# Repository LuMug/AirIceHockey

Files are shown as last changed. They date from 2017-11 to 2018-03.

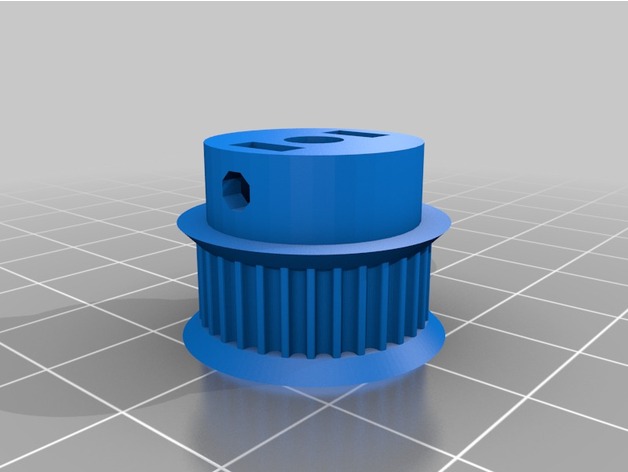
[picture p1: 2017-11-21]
Documenti_Esterni/Evo_Parts/images/PULEGGIA_MOTORE.jpg

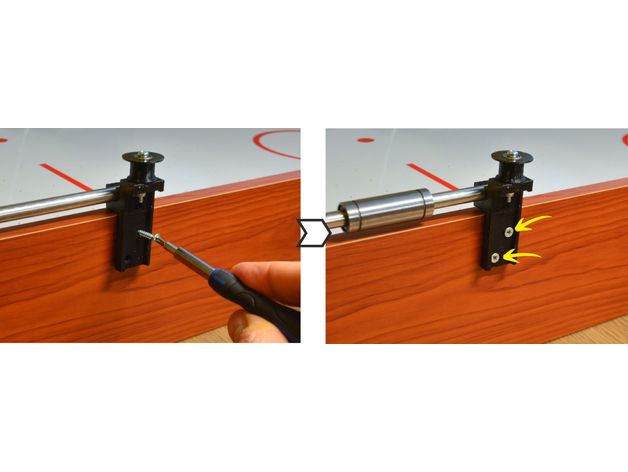
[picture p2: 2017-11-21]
Documenti_Esterni/Evo_Parts/images/Particolare_Supporto_Pulegge.jpg

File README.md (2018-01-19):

# Air Ice Hockey
### Descrizione
Si tratta di realizzare un gioco di Air Ice Hockey che permetta ad un giocatore di giocare contro un sistema robotizzato costituito da due motori passo-passo controllati da un Arduino.
Arduino riceve i comandi da un programma di visione 3D tramite una web cam oppure sfruttando un’applicazione su uno smartphone e la camera dello stesso.
### Docenti Responsabili
* Luca Muggiasca
* Adriano Barchi
### Lavoratori
* Alessia Sarak
* Joey Biancardi
* Alessandro Spagnuolo
* Giairo Mauro
## Info
**Inizio:** 10.11.2017  
**Consegna:** 19.01.2018
* [Documentazione](https://github.com/LuMug/AirIceHockey/tree/master/Documenti_Esterni "Cartella documentazione")
  + [Quaderno dei compiti](https://github.com/LuMug/AirIceHockey/blob/master/Documenti_Esterni/qdc_p2_samt_2017_18-Ice_Hockey_Robot.docx "Quaderno dei compiti")
  + [Motori passo-passo](https://github.com/LuMug/AirIceHockey/tree/master/Documenti_Esterni/Stepper_Motors "Cartella motori passo passo")
  + [Foto di montaggio](https://github.com/LuMug/AirIceHockey/tree/master/Documenti_Esterni/Evo_Parts/images "Montaggi")
* [Programmi Arduino](https://github.com/LuMug/AirIceHockey/tree/master/Programmi%20Arduino%20-%20Motori%20e%20WiFi "Cartella programmi")
  + [Programma JJRobots](https://github.com/LuMug/AirIceHockey/tree/master/Programmi%20Arduino%20-%20Motori%20e%20WiFi/AHRobot_EVO "Programma JJRobots")
  + [Programma timer](https://github.com/LuMug/AirIceHockey/blob/master/Programmi%20Arduino%20-%20Motori%20e%20WiFi/timer.ino "Programma timer")
  + [Schema elettrico timer](https://github.com/LuMug/AirIceHockey/blob/master/Programmi%20Arduino%20-%20Motori%20e%20WiFi/timer_schema.fzz "Schema elettrico timer")
* [Trello Project Management](https://trello.com/b/uI6cxGCE/airicehockey "Trello")
* [GitHub Repository](https://github.com/LuMug/AirIceHockey "GitHub Progetto")
## Diari
* [Diari](https://github.com/LuMug/AirIceHockey/tree/master/Diari "Diari")

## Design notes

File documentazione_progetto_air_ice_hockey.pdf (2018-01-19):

### Scuola Arti e Mestieri Trevano

### Sezione informatica

Titolo del progetto: | Air Ice Hockey
Alunni: | Alessia Sarak, Giairo Mauro, Joey Biancardi, Alessandro Spagnuolo
Classe: | Info I3
Anno scolastico: | 2017/2018
Docenti responsabili: | Luca Muggiasca e Adriano Barchi

# Air Ice Hockey

### SAMT – Sezione Informatica

Pagina 2 di 17

### Air Ice Hockey

Alessia, Giairo, Joey, Alessandro | Air Ice Hockey | Versione: 19.01.2018

Pagina 3 di 17

### 1 Introduzione

### 1.1 Informazioni sul progetto

Il progetto consiste nel fare un campo da Air Ice Hockey dove l’avversario è il computer. Esso deve saper rispondere all’avversario in tempo reale.
Il gruppo responsabile del progetto è composto da:
- Alessia Sarak della I3AA
- Giairo Mauro della I3BB
- Joey Biancardi della I3BB
- Alessandro Spagnuolo della I3BB
I docenti responsabili del progetto sono Adriano Barchi e Luca Muggiasca.

### 1.2 Abstract

The purpose of this project is to have an ice air hockey table that function.
This game is compost of two players; one is the computer and one is the person. The Computer part will be programming with Arduino mega.
There is an application that already exist (JJRobots), it will take the data of the table and the disk and, with Wi-Fi connection, it will send all data on our program. The data will be interpreted from the program and then the program will make his move. This move must be instantaneous and the program must decide which strategy use. There are 3 strategies: attack, defence and attack and defence.
The computer will answer in real time.

### 1.3 Scopo

Lo scopo del progetto è di creare un campo funzionante di Air Ice Hockey. Il gioco è composto da due giocatori: il computer e la persona.
Il computer dev’essere in grado di rispondere ai colpi dell’avversario in tempo reale tramite una webcam che legge i valori del disco e calcola la direzione in cui andrà, in questo modo riesce a capire dove muovere il robot, in modo che sia del tutto autonomo una volta fatta partire l’applicazione.

Analisi

### 1.4 Analisi del dominio

Abbiamo un campo da air hockey classico per 2 giocatori.
Quello che dobbiamo creare è già stato creato come progetto, JJRobots, e noi dobbiamo replicarlo usando i pezzi che i professori ci hanno dato.
L’idea del progetto è presentarlo a espoprofessioni agli interessati alla nostra scuola e in particolare alla nostra sezione (Scuola Arti e Mestieri di Trevano, sezione informatici).
Ci sarà un solo giocatore che si sfida con un sistema robotizzato che si muove grazie ad Arduino. Il come è spiegato nella sezione “scopo” e nel capitolo “implementazione”.
Per poter implementare questo progetto bisogna avere delle buone conoscenze su Arduino e bisogna conoscere come far funzionare i motori con la scheda di JJRobots per poi poterle applicare alla programmazione.

Pagina 4 di 17

### 1.5 Analisi e specifica dei requisiti

ID | REQ-001
Nome | Tavolo
Priorità | 1
Versione | 1.0
Note | -
Sub-ID | Sviluppo
001 | I componenti che muovono il robot sono montati e funzionali
002 | Accanto al punteggio c'è il segnatore di tempo rimanente
ID | REQ-002
Nome | Strategie di gioco
Priorità | 1
Versione | 1.0
Note | -
Sub-ID | Programmazione
001 | Nel programma devono essere presenti 3 strategie di gioco
002 | Strategia 1: Difesa
003 | Strategia 2: Attacco
004 | Strategia 3: Difesa - Attacco
ID | REQ-003
Nome | Movimento computer
Priorità | 1
Versione | 1.0
Note | -
Sub-ID | Programmazione
001 | Il telefono che inquadra il campo da gioco deve essere collegato con il programma
002 | Vengono registrati i dati del disco in movimento
003 | I dati vengono utilizzati per definire quale strategia di gioco utilizzare
004 | Viene attivata la strategia di gioco

### 1.6 Pianificazione

Il Gannt è suddiviso in giorni e ogni giorno è diviso in tre: le prime 2 ore, le seconde 2 ore e le terze 2 ore. Ogni colore rappresenta un membro del gruppo; il rosa rappresenta Alessia Sarak, il verde rappresenta Joey Biancardi, il blu rappresenta Giairo Mauro e il giallo rappresenta Alessandro Spagnuolo.
Il 19 gennaio è libero nel caso di qualche ritardo o nel caso si volesse perfezionare qualcosa.

Pagina 5 di 17

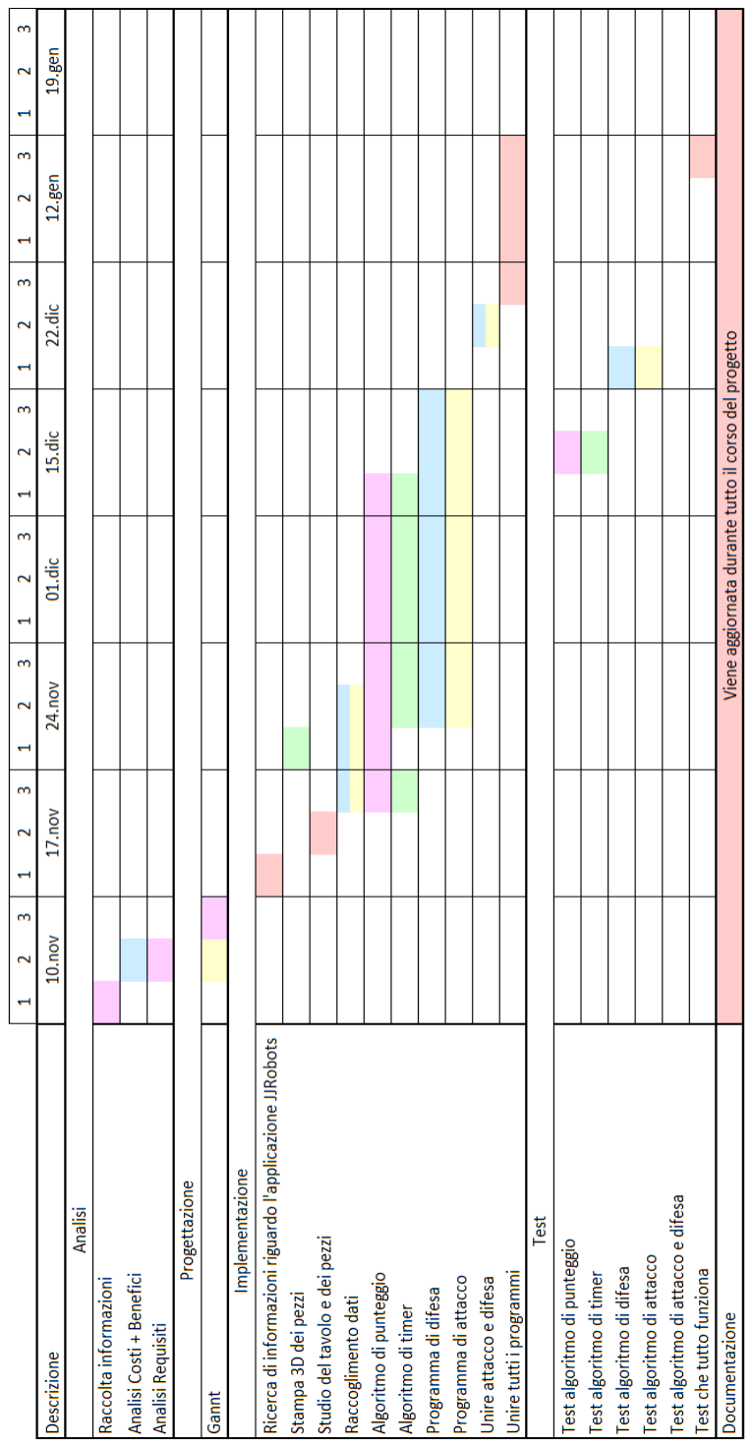
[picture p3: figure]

Pagina 6 di 17

### 1.7 Analisi dei mezzi

A disposizione c’è un tavolo per il gioco, la stampante 3D per stampare i pezzi da montare sul tavolo, l’applicazione JJRobots per prendere le misure del tavolo, una 7 segmenti Adafruit per segnalare il tempo alla fine del gioco e il nostro portatile.

### 1.7.1 Software

- Arduino IDE (programma)
- AHR Robot (JJRobots)
- Word (documentazione e diari)
- Excel (Gannt)
- Google Chrome (come visualizzatore di pdf e per le ricerche)
- PowerPoint (presentazione)
- Fritzing (schema montaggio di arduino)

### 1.7.2 Hardware

Il prodotto verrà sviluppato su un campo da Air Ice Hockey. La base è identica a quella di un campo normale, la differenza sta nel campo dell’avversario che, essendo computerizzato, ha un pusher montato su delle sbarre, esse sono collegate a delle cinghie. Per permettere il movimento del pusher sono necessari anche la scheda di JJRobots, 2 motori passo-passo, e per definire la direzione del movimento si necessita di un telefono (sistema operativo android) che tramite l’applicazione di JJRobots (Air Hockey) riesce a prevedere il movimento che verrà fatto dal puck.

Lista dei pezzi utilizzati (per vedere come montarli tra di loro andare sotto implementazione, pagina 7):
- Tavolo
- 1 – Tavolo da Air Ice Hockey
- 2 – Pusher
- 1 – Puck
- 2 – Sbarre
- 1 – Cinghia
- 2 – Motori passo-passo
- 1 – Telefono (sistema operativo Android) con su l’applicazione di JJRobots (Air Hockey)
- Timer
- 1 – Arduino Uno
- 1 – 7 segmenti Adafruit
- 2 – Resistenze
- 1 – Led Blu
- 1 – Bottone
- Programma con Arduino
- Arduino Leonardo

Pagina 7 di 17

### 2 Implementazione

Per poter fare il tavolo di Air Ice Hockey funzionante il lavoro è stato suddiviso in 3 parti: motori, algoritmo di timer e montaggio del tavolo, rispettivamente ci hanno lavorato Giairo Mauro e Alessandro Spagnuolo, Alessia Sarak, Joey Biancardi.

Motori

Componenti utilizzati

- 1 Arduino Mega (serve Arduino Leonard)
- 2 motori Stepper Motor
- 2 A4988 Stepper Motor Driver
- 1 Scheda JJRobots

Montaggio

Abbiamo montato un radiatore su ogni Driver per evitare il riscaldamento di essi, una volta fatto abbiamo collegato i due driver alla scheda JJRobots.

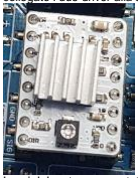
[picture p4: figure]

I cavi del motore sono stati saldati a dei componenti e poi collegati alla scheda, i cavi sono stati saldati secondo un ordine preciso mostrato nel Datasheet dei motori.

Una volta finito il montaggio della scheda JJRobots l’abbiamo collegata all’arduino fornitoci (arduino mega 2560) come mostrato nella foto seguente.

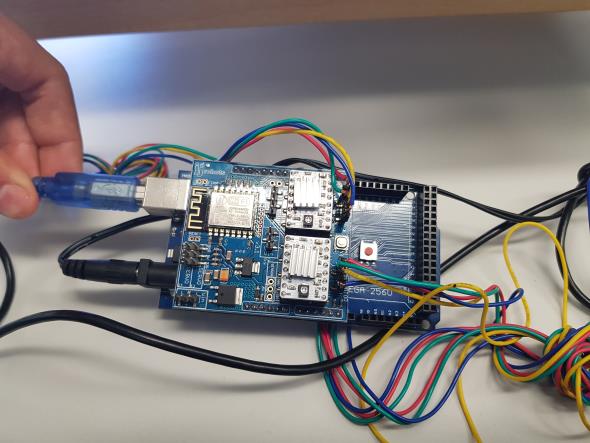
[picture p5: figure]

Pagina 8 di 17

Test motori
Attributi:
- | const int enaM1M2Pin = 4; | → pin per l’abilitazione dei due motori
- | const int microStepPin = A4; | → pin per suddivisione dei passi in micro passi
- | const int pushButtonPin = A3; | → pin per il Pulsante sul board
- | int Val = 0; | → variabile per la lettura pulsante
- | const int stepM1Pin = 7; | → Pin per step motore 1
- | const int dirM1Pin = 8; | → Pin per direzione motore 1
- | const int stepM2Pin = 12; | → Pin per step motore 2
- | const int dirM2Pin = 5; | → Pin per direzione motore 2
Il programma fa fare un giro in avanti e uno indietro ai motori, ma se si preme il bottone presente sulla scheda JJRobots fa solo un giro in una direzione.

digitalWrite(dirM1Pin, HIGH); → Inizialmente si abilita la direzione in cui si vogliono muovere i motoricon questo comando: con “HIGH” si muove in avanti con “LOW” si muove indietro.

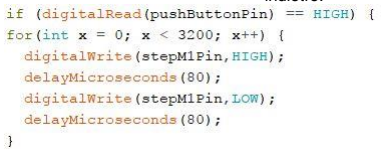
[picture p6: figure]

→ | Con il primo if si dice che quando si preme il bottone i motori devono muoversi anche in avanti.

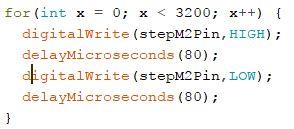
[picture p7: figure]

→ | In questo for si fa girare il motore per un gio conpleto con 3200 impulsi.

Con questi codici si può creare il progetto.

Programma per JJRobots

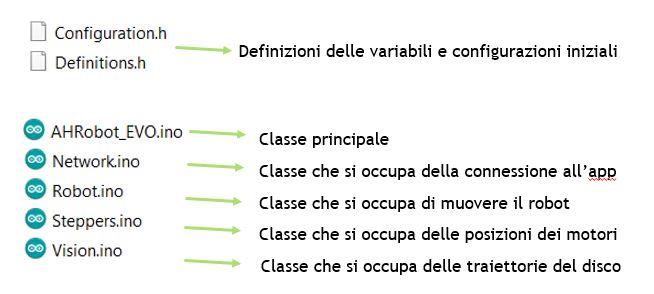
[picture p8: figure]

Le classi utilizzate per il progetto le abbiamo scaricate dal sito di JJRobots e sono le seguenti:

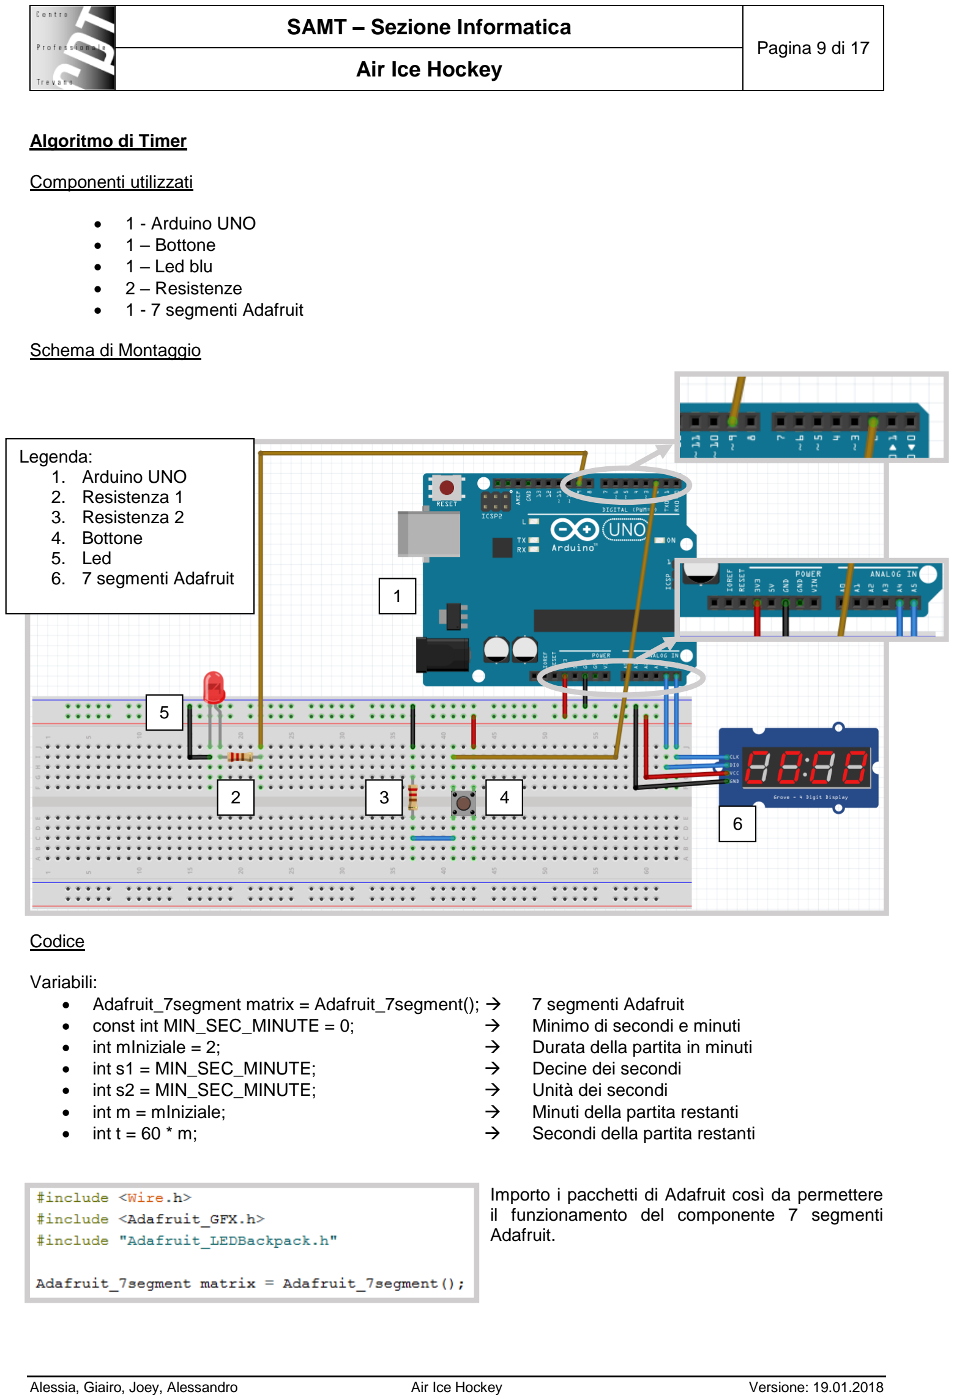
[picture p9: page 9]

Pagina 9 di 17

Algoritmo di Timer

Componenti utilizzati

- 1 - Arduino UNO
- 1 – Bottone
- 1 – Led blu
- 2 – Resistenze
- 1 - 7 segmenti Adafruit

Schema di Montaggio

Codice

Variabili:
- | Adafruit_7segment matrix = Adafruit_7segment(); → | 7 segmenti Adafruit
- | const int MIN_SEC_MINUTE = 0; | → | Minimo di secondi e minuti
- | int mIniziale = 2; | → | Durata della partita in minuti
- | int s1 = MIN_SEC_MINUTE; | → | Decine dei secondi
- | int s2 = MIN_SEC_MINUTE; | → | Unità dei secondi
- | int m = mIniziale; | → | Minuti della partita restanti
- | int t = 60 * m; | → | Secondi della partita restanti

Importo i pacchetti di Adafruit così da permettere il funzionamento del componente 7 segmenti Adafruit.

5

2

1

3 | 4
6

Legenda:
1. Arduino UNO
2. Resistenza 1
3. Resistenza 2
4. Bottone
5. Led
6. 7 segmenti Adafruit

5

6

1

2 | 3 | 4

Pagina 10 di 17

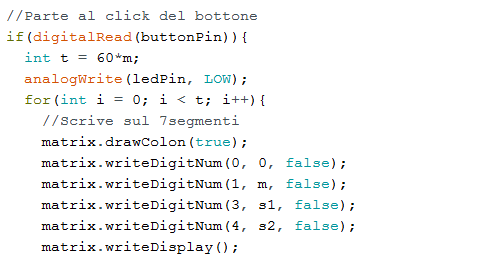
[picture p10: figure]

Quando il bottone viene schiacciato parte il conto alla rovescia.
Spengo il led che segna la fine della partita.
Il for si ripete per il numero di secondi necessari.

matrix.drawColon(bool);
Definisce se i due punti “ : “ devono venire segnati o meno.

matrix.writeDigit(colonna, numero 0 – 9, bool); Colonna: in quale casella devo scriverci su. Numero: valore da scriverci.
Bool: se il punto del rispettivo numero è acceso o spento.

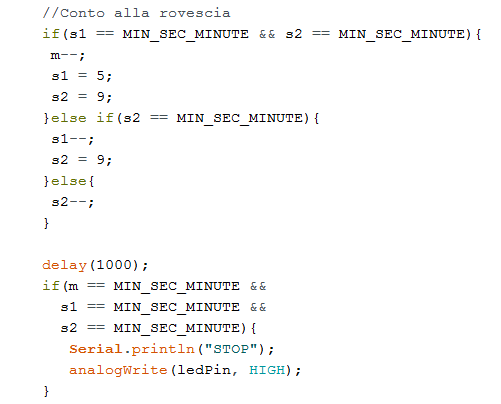
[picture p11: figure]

Faccio il conto alla rovescia sottraendo i vari valori; quando sono tutti a 0 si ferma il tempo, quando i secondi (s1, s2) vanno a 0 si sottrae un minuto (m) al tempo totale, se le unità (s2) vanno a 0 si sottrae uno alle decine (s1) e si fa tornare le unità a 9, altrimenti si sottrae uno alle unità (s2).

Delay(1000) serve per far passare un secondo tra una sottrazione e l’altra.

Finito il delay controllo se il tempo è finito e se lo è accendo il led per rendere più visibile la fine.

Pagina 11 di 17

Montaggio Tavolo

La parte che permette a tutto il progetto di essere operativo e assemblato è il tavolo da gioco, costruito appositamente per l’air ice hockey, fornito di ventola per l’aria e di linee per il gioco.
Un tavolo a cui mancano diversi componenti come i motori per permetterne il funzionamento.

I pezzi utilizzati sono stati i seguenti:

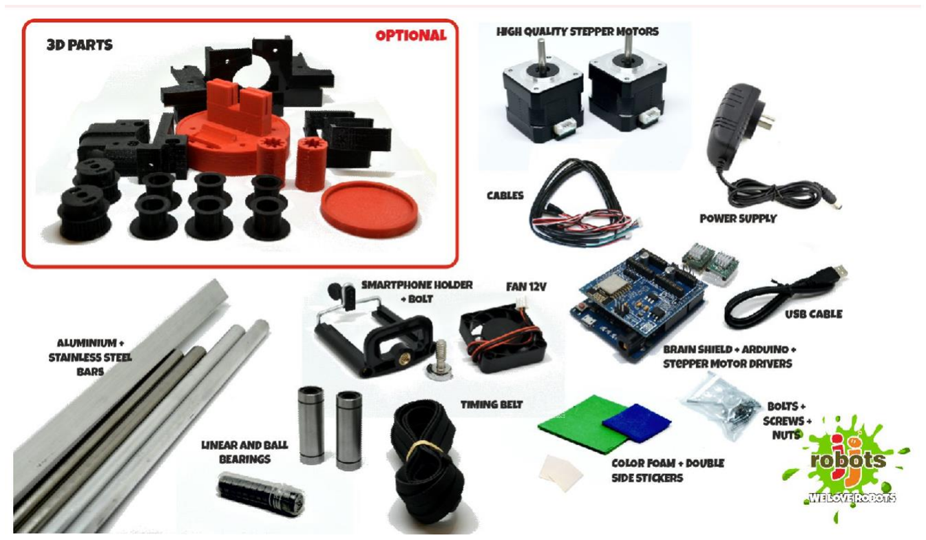
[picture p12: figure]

Il primo passo da effettuare è l’assemblaggio dei motori. → Materiale necessario: 6x 6mm M3 bolts.

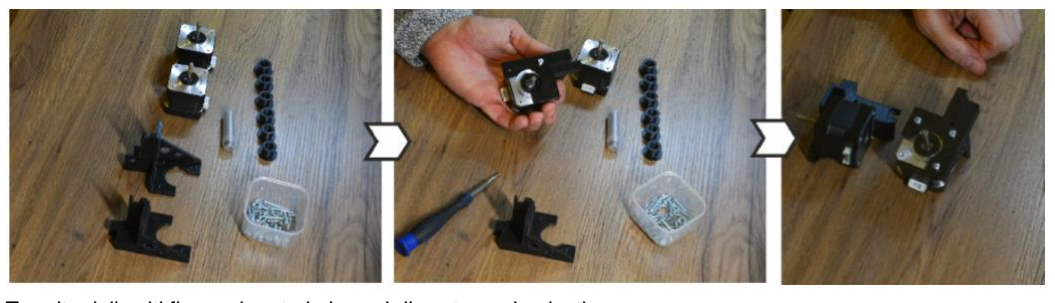
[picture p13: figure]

Tramite delle viti fissare i motori ai pezzi di sostegno in plastica.

Successivamente, vanno preparate le pulegge:
→ Materiale necessario: 12x cuscinetti a sfera 623, 6x 25mm bolt, 6x pulegge.

L’assemblaggio delle sei pulegge va fatto seguendo la seguente illustrazione:

Pagina 12 di 17

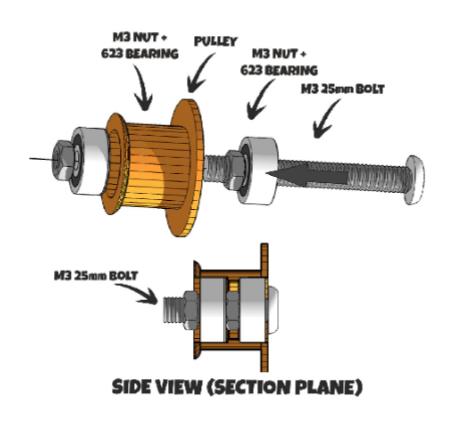
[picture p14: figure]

Il passo successivo da fare riguarda l’assemblaggio della sbarra che sostiene il nemico del gioco: → Materiale necessario: due sbarre in alluminio, due pezzi in plastica che permettono lo scorrimento del nemico sulle sbarre, due cuscinetti per lo scorrimento di tutto l’assemblaggio perpendicolare alla visione del giocatore che verranno messi all’interno di due pezzi in plastica in cui verranno infilate le sbarre, il pezzo in plastica per il nemico.

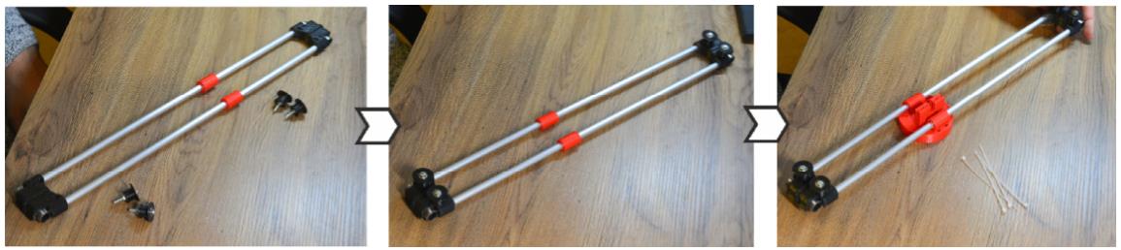
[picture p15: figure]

Per fare bene questa parte è molto importante fissare con attenzione il pezzo del nemico alle sbarre:

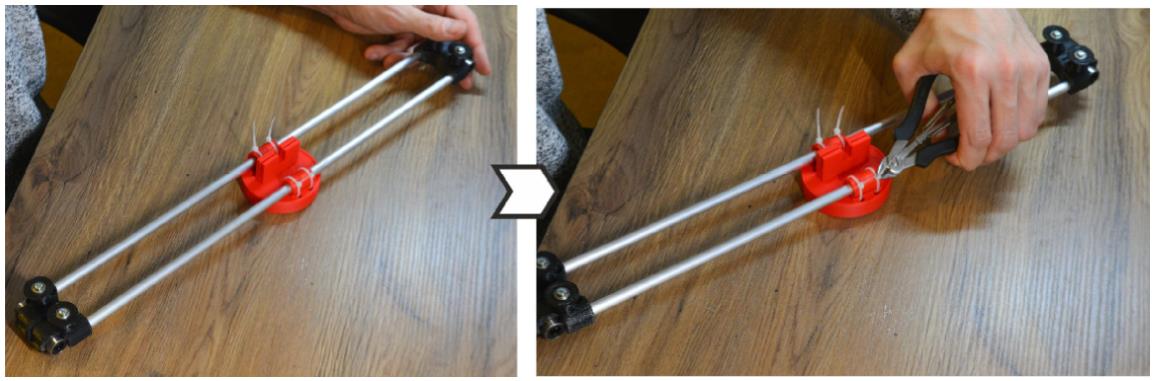
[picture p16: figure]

Pagina 13 di 17

Sotto al pezzo del nemico, va incollata una superficie colorata che ne permette il riconoscimento da parte dell’Arduino.

Adesso devono essere preparate le pulegge da
attaccare ai motori:

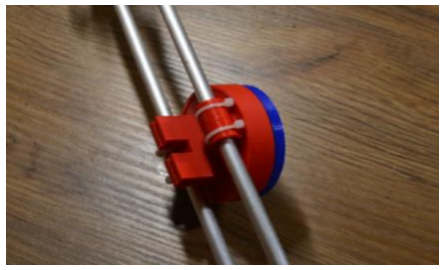
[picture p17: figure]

→ Materiale necessario: 4x 15mm bolts, pezzi che permetteranno alla cinghia di girare.

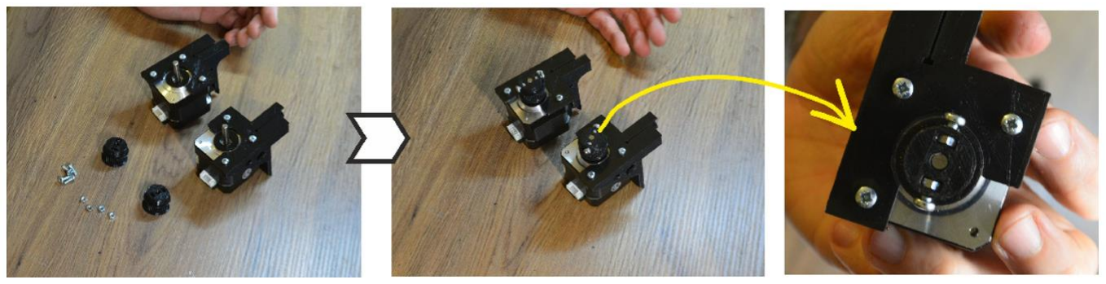
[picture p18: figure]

Passiamo a ciò che andrà fissato ai lati del tavolo per far muovere la sbarra centrale: → Materiale necessario: 4x M3 10mm bolts, 4 nuts.

Seguire il procedimento di montaggio come da illustrazione.

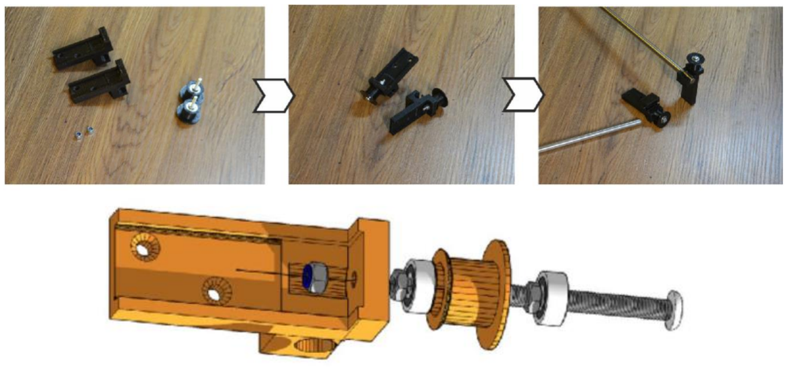
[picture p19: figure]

Il prossimo passo è molto semplice, si tratta solamente di inserire le sbarre in alluminio all’interno dei sostenitori che verranno poi fissati ai lati del tavolo, per farlo basta seguire le figure sottostanti.

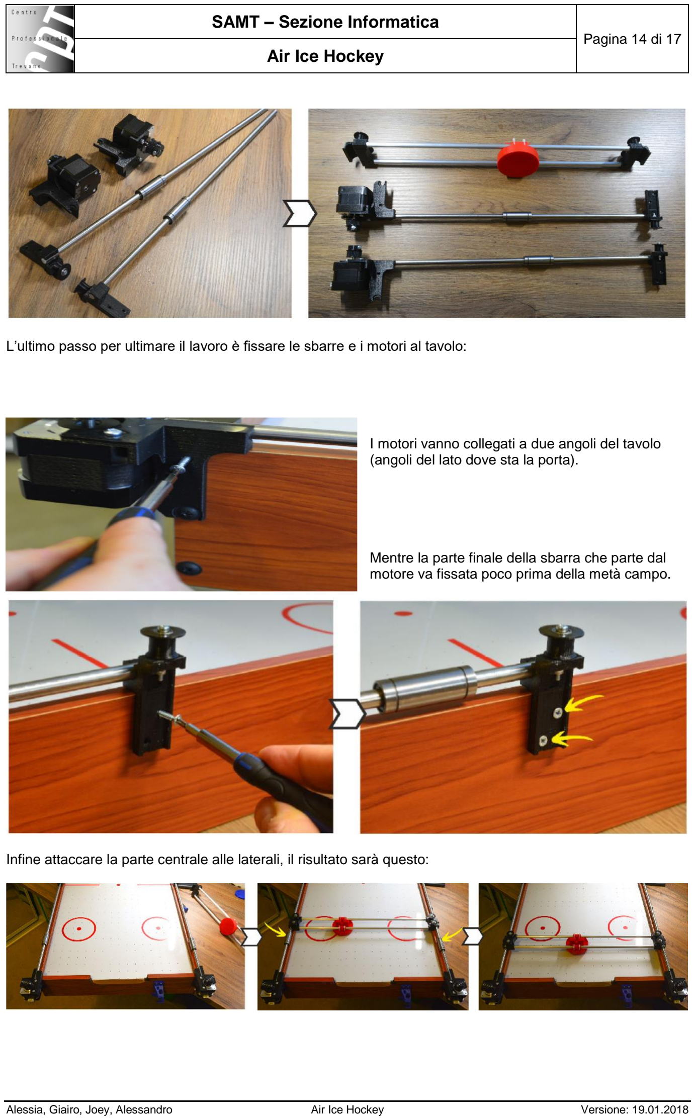
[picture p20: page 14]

Pagina 14 di 17

L’ultimo passo per ultimare il lavoro è fissare le sbarre e i motori al tavolo:

I motori vanno collegati a due angoli del tavolo (angoli del lato dove sta la porta).

Mentre la parte finale della sbarra che parte dal motore va fissata poco prima della metà campo.

Infine attaccare la parte centrale alle laterali, il risultato sarà questo:

Pagina 15 di 17

### 3 Test

### 3.1 Protocollo di test

Test Case: | TC-001 | Nome: | Test funzionamento timer
Descrizione: | Quando viene schiacciato il bottone il timer parte e all’arrivo dello 0 si accende il led, per segnalare la fine, e il timer ritorna al valore iniziale.
Prerequisiti: | Nessuno.
Procedura: | 1. Schiacciare il bottone
Risultati attesi: | Il timer parte e quando arriva a 0 si accende il led per segnalare che il tempo è finito e ritorna al valore iniziale.
Test Case: Riferimento: | TC-002 REQ-002 | Nome: | Test motori e applicazione JJRobots
Descrizione: | Testare il funzionamento dei motori e il collegamento dell’applicazione con Arduino e l’acquisizione dei dati da parte della telecamera.
Prerequisiti: | Applicazione scaricata su un telefono Android, motori collegati all’Arduino.
Procedura: | 1. Collegare il telefono alla rete Wi-Fi di JJRobots 2. Aprire l’applicazione AirHockey Robot 3. Calibrare i colori e il tavolo 4. Cliccare il bottone start 5. Caricare il codice su Arduino
Risultati attesi: | Il robot si muove grazie ai motori in base alla traiettoria del disco

### 3.2 Mancanze/limitazioni conosciute

Il progetto non funziona perché ci mancava l’Arduino giusto, noi abbiamo utilizzato il mega quando c’era in realtà bisogno dell’Arduino Leonardo.
La differenza sta nel fatto che l’Arduino prova a leggere i dati dalla scheda dal serial1 ma il serial1 non è collegato alla scheda.

Pagina 16 di 17

### 4 Consuntivo

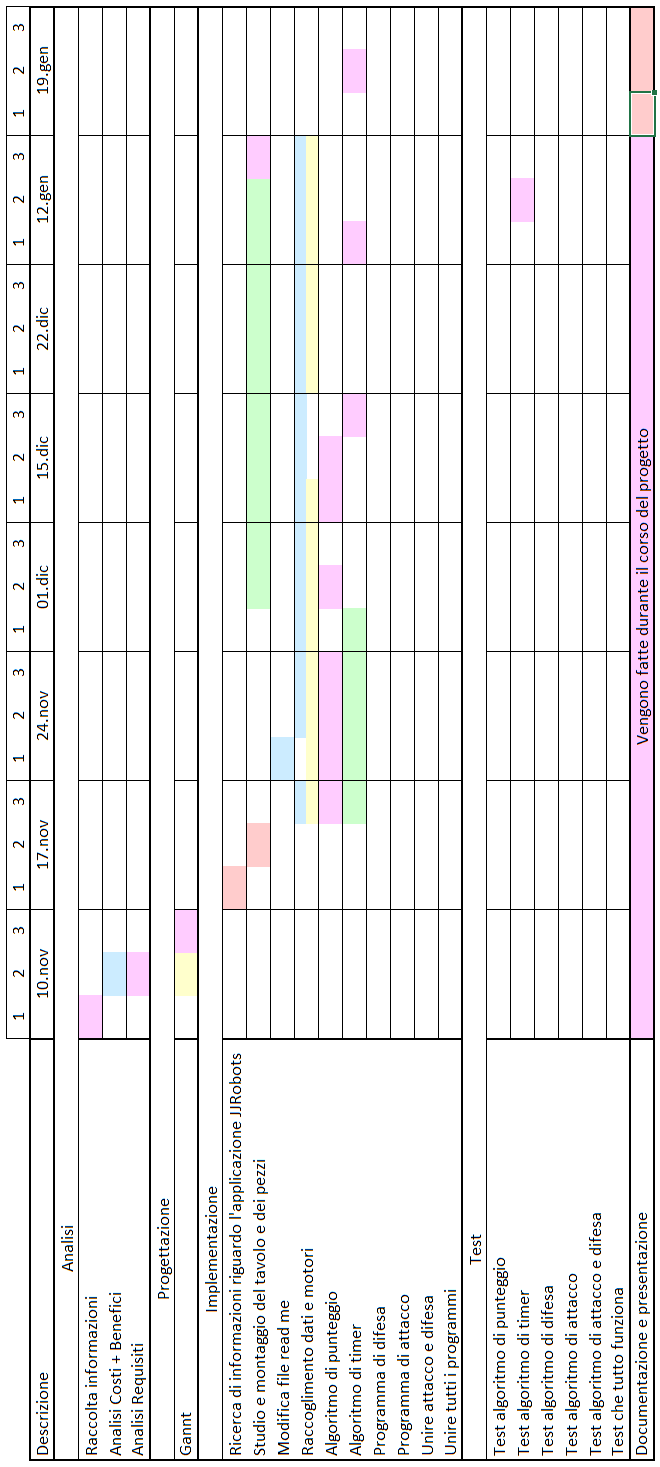
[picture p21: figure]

Pagina 17 di 17

### 5 Conclusioni

All’inizio il progetto ci è sembrato molto interessate e fattibile, gli elementi indicati da avere erano chiari, il problema è stato che non ci è stato assegnato l’Arduino Leonardo, quello corretto per poter fare il progetto, quindi non è stato possibile finirlo. Sono state fatte diverse ricerche per fare funzionare l’Arduino Mega al posto di quello Leonardo ma sono state inutili, quindi non funziona nulla eccetto il timer.
Eccetto questo il progetto è stato interessante.

### 5.1 Sviluppi futuri

Non avendo l’Arduino giusto, il prossimo sviluppo prevede di mettere l’Arduino Leonardo e il punteggio verrà fatto tramite dei bottoni messi vicino al giocatore.

### 5.2 Considerazioni personali

Non avendo i pezzi corretti abbiamo imparato che bisogna seguire ciò che c’è scritto ed insistere nel caso non ci vengano assegnate le cose corrette.

### 6 Allegati

- Diari di lavoro
- Codici

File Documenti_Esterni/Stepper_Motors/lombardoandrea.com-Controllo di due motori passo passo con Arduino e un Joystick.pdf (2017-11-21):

Andrea | 25/5/2017

# Controllo di due motori passo passo con Arduino e un Joystick

lombardoandrea.com/motori-passo-passo-arduino-joystick/

Tempo di Arduino e motori passo passo. In questo post ti faccio vedere come è possibile realizzare un sistema di controllo di due motori passo passo con Arduino e un Joystick. A fine pagina trovi il video con la dimostrazione. Come mostrato in un precedente articolo, (http://www.lombardoandrea.com/pilotare-un-motore-passo-passo-con-arduino-e-il-driver-a4988/) una delle migliori soluzioni per pilotare un motore passo passo tramite Arduino è quella di utilizzare dei driver adatti. Ultimamente sto usando dei moduli Pololu A4988 semplici, completi ed affidabili.
Sono progettati per poter comandare i motori in modalità full-, half-, quarter-, eighth-, e sixteenth-step. Ovvero è possibile far ruotare l’asse del motore di uno step completo oppure di 1/2, 1/4, 1/8 e 1/16. Questa funzionalità fa si che i movimenti del motore siano più o meno fluidi e precisi a seconda delle nostre esigenze.
La semplicità di utilizzo sta nel fatto che al nostro driver, in una configurazione base, basteranno solo due PIN (non considerando l’alimentazione logica) ai quali far arrivare due segnali per determinarne la velocità ed il senso di marcia del motore.
La velocità, tramite il pin STEP richiede un alternanza (pulse) di stati logici alto/basso per poter far muovere il motore, mentre tramite il pin DIR, decideremo il senso di marcia.
Maggiori dettagli e caratteristiche sul driver le trovi qui. (https://www.pololu.com/file/download/a4988_DMOS_microstepping_driver_with_translator.pdf?file_id=0J450)
Per quanto riguarda invece la parte software deputata alla gestione dei motori passo passo, AccelStepper (http://www.airspayce.com/mikem/arduino/AccelStepper/) è la libreria che fa al caso nostro.
Tornando allo scopo del post ti mostro subito il codice che come al solito è ampiamente commentato, ma se qualcosa non ti torna puoi tranquillamente usare la sezione commenti.

Il codice

1. /*
2. * Controllo di due motori passo passo con Arduino e un Joystick
3. *
4. * Autore : Andrea Lombardo
5. | * Web | : http://www.lombardoandrea.com
6. | * Post | : http://wp.me/p27dYH-KQ
7. */
8. //Inclusione delle librerie
9. #include <AccelStepper.h>
10. #include <Bounce2.h>
11. //definizione delle costanti dei pin di Arduino
12. const int ledEnable = 13; //il led on board ci mostrerà lo stato di attivazione dei motori
13. const int pinSwEnable = 7; //il bottone presente nel modulo joystick che abilita o disabilita il controllo
14. const int pinEnable = 8; //i pin che comandano lo stato ENABLE dei driver A4988 sono in collegati in serie per questo basta un solo pin per gestirli
| entrambi
15. unsigned long debounceDelay = 10; //millisecondi per il debonuce del bottone
16. const int jX = A0; //pin analogico che legge i valori per le X
17. const int stepX = 3; //pin digitale che invia i segnali di STEP al driver

17. const int stepX = 3; //pin digitale che invia i segnali di STEP al driver delle X
18. const int dirX = 4; //pin digitale che invia il segnale DIREZIONE al driver delle X
19. long speedX, valX, mapX; //variabili di gestione movimenti motore X
20. const int jY = A1; //pin analogico che legge i valori per le Y
21. const int stepY = 5; //pin digitale che invia i segnali di STEP al driver delle Y
22. const int dirY = 6; //pin digitale che invia il segnale DIREZIONE al driver delle Y
23. long speedY, valY, mapY; //variabili di gestione movimenti motore Y
24. //variabili utilizzate dalla libreria AccelStepper
25. const int maxSpeed = 1000; //stando alla documentazione della libreria questo valore può essere impostato fino a 4000 per un Arduino UNO
26. const int minSpeed = 0; //velocità minima del motore
27. const float accelerazione = 50.0; //numero di step al secondo in accelerazione
28. const int treshold = 30; //la lettura dei potenziometri non è mai affidabile al 100%, questo valore aiuta a determinare il punto da considerare come "Stai fermo" nei movimenti
29. long tresholdUp, tresholdDown; //variabili di servizio per espletare il compito descritto sopra
30. boolean abilitato, muoviX, muoviY, enable; //variabili di gestione dei movimenti
31. Bounce btnEnable = Bounce(); //istanzia un bottone dalla libreria Bounce
32. //istanzia i motori
33. AccelStepper motoreX(AccelStepper::DRIVER, stepX, dirX);
34. AccelStepper motoreY(AccelStepper::DRIVER, stepY, dirY);
35. void setup() {
36. //inizializza valori
37. speedX = speedY = 0;
38. enable = false;
39. //definizione delle modalità dei pin
40. pinMode(ledEnable, OUTPUT);
41. pinMode(pinEnable, OUTPUT);
42. pinMode(pinSwEnable, INPUT_PULLUP); //l'input dello switch ha bisogno di essere settato come INPUT_PULLUP
43. digitalWrite(ledEnable, enable);
44. digitalWrite(pinEnable, !enable); //I driver A4988 disabilitano i comandi al motore se sul pin ENABLE ricevono un segnale HIGH per questo motivo il valore è opposto a quello del LED
45. //configura il bottone del joystick utilizzando la libreria Bounce
46. btnEnable.attach(pinSwEnable);
47. btnEnable.interval(debounceDelay);
48. //calcola range valori entro i quali considerare la posizione del joystick come "Stai fermo"
49. tresholdDown = (maxSpeed / 2) - treshold;
50. | tresholdUp = (maxSpeed / 2) + treshold; | 2/40

50. tresholdUp = (maxSpeed / 2) + treshold;
51. //configura parametri dei motori
52. motoreX.setMaxSpeed(maxSpeed);
53. motoreX.setSpeed(minSpeed);
54. motoreX.setAcceleration(accelerazione);
55. motoreY.setMaxSpeed(maxSpeed);
56. motoreY.setSpeed(minSpeed);
57. motoreY.setAcceleration(accelerazione);
58. }
59. void loop() {
60. //esegui funzione di controllo e lettura del bottone che determina lo stato di abilitazione
61. checkEnable();
62. digitalWrite(ledEnable, enable); //mostra stato di abilitazione tramite il led su pin 13
63. digitalWrite(pinEnable, !enable); //imposta valore opposto sui pin ENABLE dei driver
64. //esegui lettura analogica dei valori provenienti dai potenziometri del joystick
65. valX = analogRead(jX);
66. valY = analogRead(jY);
67. //mappa i valori letti in funzione della velocità inima e massima
68. mapX = map(valX, 0, 1023, minSpeed, maxSpeed);
69. mapY = map(valY, 0, 1023, minSpeed, maxSpeed);
70. //esegui funzione di comando dei motori
71. pilotaMotori(mapX, mapY);
72. }
73. void pilotaMotori(long mapX, long mapY) {
74. if (mapX <= tresholdDown) {
75. //x va indietro
76. | speedX = -map(mapX, tresholdDown, minSpeed, | minSpeed, maxSpeed);
77. muoviX = true;
78. } else if (mapX >= tresholdUp) {
79. //x va avanti
80. speedX = map(mapX, maxSpeed, tresholdUp, maxSpeed, minSpeed);
81. muoviX = true;
82. } else {
83. //x sta fermo
84. speedX = 0;
85. muoviX = false;
86. }
87. if (mapY <= tresholdDown) {
88. //y va giù
89. | speedY = -map(mapY, tresholdDown, minSpeed, | minSpeed, maxSpeed);

90. muoviY = true;
91. } else if (mapY >= tresholdUp) {
92. //y va su
93. speedY = map(mapY, maxSpeed, tresholdUp, maxSpeed, minSpeed);
94. muoviY = true;
95. } else {
96. //y sta fermo
97. speedY = 0;
98. muoviY = false;
99. }
100. if (muoviX) {
101. motoreX.setSpeed(speedX);
102. motoreX.run();
103. } else {
104. motoreX.stop();
105. }
106. if (muoviY) {
107. motoreY.setSpeed(speedY);
108. motoreY.run();
109. } else {
110. motoreY.stop();
111. }
112. }
113. void checkEnable() {
114. btnEnable.update();
115. if (btnEnable.fell()) {
116. enable = !enable;
117. }
118. }

Come avrai notato, ho utilizzato un’altra libreria nel codice. Si chiama Bounce2 ed è utilissima nella gestione dei bottoni. Per maggiori informazioni ti rimando alla sua pagina GitHub. (https://github.com/thomasfredericks/Bounce2/)

Lo schema dei collegamenti

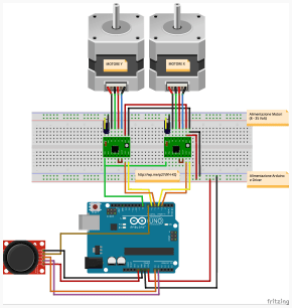
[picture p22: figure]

Schema Arduino Joystick 2 Stepper Motor

Attenzione: il joystick mostrato nello schema dei collegamenti è diverso da quello utilizzato nel video, pertanto la posizione fisica dei pin è diversa.
In ogni caso ricorda che Vcc e GND (joystick) vanno collegati rispettivamente a +5 e GND (Arduino) mentre i pin analogici per i valori di X e Y vanno sui pin A0 e A1 ed il restante pin digitale dello switch va sul pin D7.

Come sempre

Assicurati che tutti i collegamenti siano corretti; Ricordati di impostare la porta COM del tuo Arduino; Utilizza le tensioni corrette;

E ricorda che io non mi assumo nessuna responsabilità per eventuali danni o disastri che causi

Prodotti Amazon

Modulo joystick KY-023 due assi X-Y joypad resistivo PS2 arduino raspberry (https://www.amazon.it/Modulo-joystick-resistivo-arduino-raspberry/dp/B01N1RXLY3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)

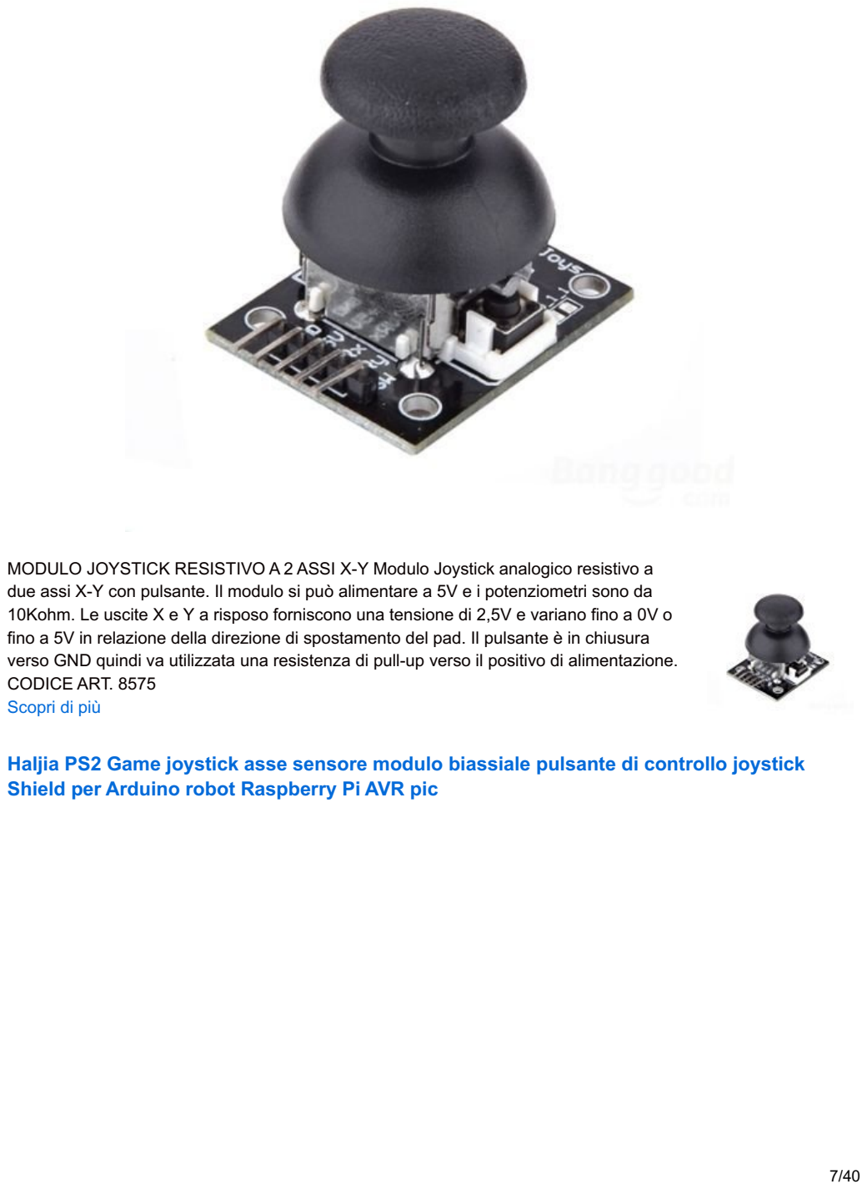
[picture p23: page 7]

MODULO JOYSTICK RESISTIVO A 2 ASSI X-Y Modulo Joystick analogico resistivo a due assi X-Y con pulsante. Il modulo si può alimentare a 5V e i potenziometri sono da 10Kohm. Le uscite X e Y a risposo forniscono una tensione di 2,5V e variano fino a 0V o fino a 5V in relazione della direzione di spostamento del pad. Il pulsante è in chiusura verso GND quindi va utilizzata una resistenza di pull-up verso il positivo di alimentazione. CODICE ART. 8575
Scopri di più

Haljia PS2 Game joystick asse sensore modulo biassiale pulsante di controllo joystick Shield per Arduino robot Raspberry Pi AVR pic (https://www.amazon.it/PS2-Game-joystick-biassiale-controllo-Raspberry/dp/B06Y1HB7KR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)

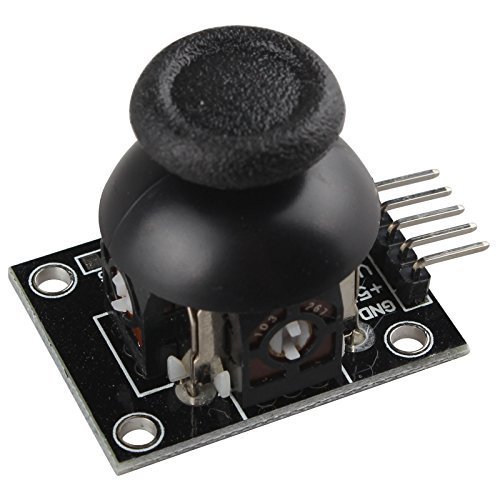
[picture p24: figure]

Questo è il modulo joystick gioco PS2 per Arduino Un sacco di progetti di robot hanno bisogno di joystick. Questo modulo fornisce una soluzione conveniente per quello. Basta collegarsi a due ingressi analogici, il robot è ai vostri comandi con x, y il controllo. Essa ha anche un interruttore che è collegato ad un perno digitale. Questo modulo joystick può essere facilmente connettersi a Arduino da normale Shield espansione iO con cavi in?? Nessuna saldatura richiesta, riutilizzabile per la prototipazione e progettazione applicazioni di circuito elettronico, modificare o rivedere i circuiti facilmente. Accetta resistenze, transistor, diodi, LED, condensatori e altri tipi di componenti elettronici. Uno strumento prezioso per la sperimentazione di circuiti disegni sia nel settore della R & S. movimenti direzionali sono semplicemente due potenziometri - uno per ogni asse Compatibile con interfaccia Arduino Tre assi (x, y, Z (tasto)) Dimensioni: 37 x 25 x 32 mm Peso: 15 g Materiale plastico ABS Completamente riutilizzabile Bronzo fosforoso nichelato clip a molla Accetta una varietà di dimensioni dei cavi (AWG 29 - 20) Lista di imballaggio: 1 x Modulo joystick
Scopri di più

KY-023 PS2 Joystick Breakout Modulo gioco Rocker Sensore Shield XY asse per Arduino (https://www.amazon.it/KY-023-Joystick-Breakout-Sensore-Arduino/dp/B075HB55SQ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)

"Descrizione del prodotto: Caratteristiche del prodotto: KY-023 modulo di rottura joystick a doppio asse. Dotata di resistenza bidirezionale a 10K, il rubinetto varia con la modifica della direzione del joystick. La tensione di esercizio 5V e lo stato originale della tensione di lettura X, Y sono di circa 2,5V, quando premete verso il basso nella direzione della freccia, la tensione aumenta fino a 5V, preme la freccia nella direzione opposta, diminuisce la tensione, il minimo è 0V. Adatto per Arduino UNO, per Arduino UNO R3, Scheda di sviluppo Arduino 2560 per progettare le opere interattive di controllo creativo. Lista imballaggio: 1 x modulo di Breakout. Scopri di più

Bluelover 5 X Ps2 Gioco Joystick Modulo Per Arduino (https://www.amazon.it/Bluelover-Gioco-Joystick-Modulo-Arduino/dp/B074QVZKZ2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)

Descrizione: Questo è il modulo di gioco PS2 joystick per Arduino Un sacco di progetti robot bisogno di joystick. Questo modulo fornisce una soluzione a prezzi accessibili. Basta collegare a due ingressi analogici, il robot è ai vostri comandi con x, y di controllo. Ha anche un interruttore che è collegato a un pin digitale. Questo modulo joystick può essere facilmente collegato ad Arduino con il normale scudo di espansione io con i cavi in dotazione. Nessuna saldatura richiesta, riutilizzabile per la prototipazione o applicazioni di progettazione di circuiti elettronici, modificare o rivedere i circuiti facilmente. Accetti i resistori, i transistori, i diodi, i LED, i condensatori ed altri tipi di componenti elettronici. Uno strumento prezioso per sperimentare con i disegni del circuito se nel r&d. Movimenti direzionali sono semplicemente due potenziometri-uno per ogni asse Compatibile con interfaccia Arduino Marca: Keyes Modello: KY-023 Specifica: Tre assi (x, y, z (tasto)) Dimensioni: 37x25x32mm Peso: 15 g Documenti WikiDoc Tie-punto 700 Materiale plastico ABS Completamente riutilizzabile Morsetti in nichel bronzo placcati a fosforo Accetta una varietà di formati di filo (29-20 AWG) Pacchetto incluso: 5 x modulo Joystick PS2
Scopri di più

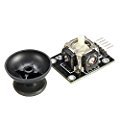
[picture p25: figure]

PS2 Joystick Breakout modulo per Arduino PIC microcontroller DIY Prototyping (https://www.amazon.it/PS2-Joystick-Breakout-Arduino-microcontroller-Prototyping/dp/B01M74LRAR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)

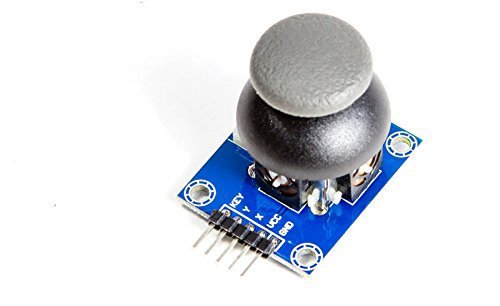
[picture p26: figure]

'PS2 joystick Break Out modulo per Arduino PIC microcontroller DIY Prototyping confronto bar o forse addirittura identico al modulo joystick di PS 2 Game Controllers. L' interruttore premere tramite pressione del joystick knüppels. Stampa della joystick coordinate è analogica e avviene tramite 2 uscite. Avete bisogno di 2 libere di interfaccia analogica al suo microcontrollore affinché possano cogliere la funzione fiscale. Queste interfacce sono con "x" e "Y" gekenntzeichnet. Per il pulsante è un digitale o analogico Input. della corrente in uscita significa "Key. Contenuto della confezione originale: 100% nuovi di zecca Voltaggio di ingresso: 5 V segnale: Analog 5 Pins 1 tasto (Funzione di stampa su il joystick bastoni) Dimensioni circa dimensioni: 29 x 34 x 35 mm Il breakout board potrebbe avere il colore nero o blu.
Scopri di più

Elegoo 5 pcs A4988 Stepstick Modulo Stepper Motor Driver + Heat Sink Radiatore per Stampanti 3D Printer Reprap, CNC Macchine, Robot o Arduino (https://www.amazon.it/Elegoo-Stepstick-Radiatore-Stampanti-Macchine/dp/B06XRGYVZJ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)


Nome Del Prodotto:Elegoo Stepstick Modulo Stepper Motor Driver A4988 + Heat Sink Radiatore per Stampanti 3D Printer, CNC Macchine, Robot o Arduino (Pacco da 5) Caratteristiche: A4988 è un complete driver microstepping motore con incassato un traslatore per semplici operazioni. Il prodotto può essere nella modalità: pieno, mezzo, 1/4, 1/8 and 1/16 step per operare con il motore stepper bipolarmente Capacità di uscita da 35V e ± 2 AA4988 include la regolazione della corrente, quindi il decadimento può essere basso o alto. Il variatore è la chiave per rendere semplice l'implementazione del A4988. Immettendo un impulse nello STEP il motore fa un microstep. Non ci sono tabelle di frequenza di fase, linee di controllo ad alta frequenza o interfaccia complesse per programmare. L'interfaccia dell' A4988 è veramente adatta mentre per microprocessori complessi è inadatta o è in sovraccarico- Le operazioni di Micro-step, Il controllo di taglio in the A4988 seleziona automaticamente la corrente( decadimento veloce o decadimento lento) Nella modalità mischiata, il dispositivo inizialmente mette il decadimento veloce e poi il decadimento lento. Questa modalità intermedia dà come risultato una riduzione del rumore dei motori, incrementando l'accuratezza degli step e riducendo il consume di energia. Circuiti di controllo interno di sincronismo per migliorare la modulazione di larghezza d'impulso (PWM) quando si utilizza. Le protezioni interne di circuito includono: Arresto termico per sovratemperatura, Blocco per sottotensione(UVLO) e la protezione di accavallamento-corrente L'A4988 monta il QFN package (ES), Le dimensioni di 5 mm × 5 mm nominal e con un'altezza di 0.90 mm, e con pad esposto per una maggiore dissipazione termica. Il pacco è Pb (suffisso-T), con 100% placcatura in latta opaca.
Scopri di più

PoPprint, stepper con dissipatori di calore, 5 pezzi, Rampa1.4 A4988, per stampanti 3D, Green, 5 (https://www.amazon.it/PoPprint-stepper-dissipatori-Rampa1-4-stampanti/dp/B06Y28H956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)


- Colori: verde, rosso. Dissipatori di calore: 9 x 9 x 5 mm. A4988: 20 x 15 x 11 mm. La confezione include: 5 x moduli driver per motori La driver board A4988 è ampiamente utilizzata su stampanti 3D e piccole macchine CNC. Interfaccia di controllo di direzione e pazzo semplice. Protezione termica, protezione di sovracorrente, protezioni con messa a terra. Cinque diversi step-mode: full, 1/2, 1/4, 1/8 and 1/16. Controllo della corrente regolabile, che consente di impostare l'uscita di corrente massima con un potenziometro, e di utilizzare tensioni superiori quella standard del moto usato, per ottenere un ratio di step superiore. -
Scopri di più

WINOMO 5pcs StepStick 4 strati DRV8825 Stepper Motor Driver modulo per stampante 3D Reprap RP A4988 (https://www.amazon.it/WINOMO-StepStick-DRV8825-Stepper-stampante/dp/B010NPM3RY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)



DescrizioneQuesto DRV8825 Stepper Motor Driver Module è l'aggiornamento di A4988, passo semplice e interfaccia di controllo di direzione, 4 strati, 2 oz di rame PCB per dissipazione di calore migliore, sei diversi passo risoluzioni: passo intero, mezzo passo, 1/4 passo, 1/8-passo, 1/16 step e permette di controllo corrente 1/32-step e AVOLINO impostare la massima corrente di uscita con un potenziometro, che consente di utilizzano tensioni superiori a tensione nominale del vostro motore passo a passo per ottenere maggiore velocità di passaggionbsp; Questo modulo di DRV8825 Stepper Motor Driver è aggiornamento di A4988. Utilizzare per sostituire il A4988 per aggiornare la stampante 3D.Caratteristiche-Regolabile controllo corrente consente di impostare la massima corrente di uscita con un potenziometro, che consente di utilizzare tensioni superiori a tensione nominale del vostro motore passo a passo per ottenere maggiore velocità di passaggio-Controllo taglia intelligente che seleziona automaticamente la corretta modalità di decadimento corrente (deperimento veloce o lento decadimento)-Tensione di alimentazione massima di V 45-Built-in regolatore (nessuna alimentazione di tensione logica esterna necessaria)-Dimensioni modulo interfaccia e pinout corrispondono a quelli del nostro A4988 stepper motor driverPacchetto che comprende5 * StepStick 4 strati DRV8825 Stepper Motor Driver modulo per stampante 3D Reprap RP A4988
Scopri di più

XCSOURCE Kit stampante 3D con V3.0 CNC Shield + ONU R3 Board + 4 pezzi A4988 motore Motore driver Passaggio con dissipatore di calore per Arduino
TE623 (https://www.amazon.it/XCSOURCE-stampante-Passaggio-dissipatore-TE623/dp/B01N1F078S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)


Caratteristiche: Brillante 3D Accessori per la stampa nel mese di settembre si riunisce la maggior parte delle esigenze. Shield V3.0 include bordo CNC ONU R3, modulo motore passo-passo A4988 StepStick. La stampante V3 3D scudo motore passo-passo può essere usato come driver scheda di espansione per macchine d'incisione e stampanti 3D. Ha totalmente 4 slot di canale per moduli di azionamento passo per la guida A4988 4 motore passo-passo del canale. Ogni motore passo-passo canale ha bisogno di solo 2 IO porti, il che significa che 8 IO porte sono sufficienti a gestire 3 stepper. Questo scudo può fare un lavoro rapido per gestire i motori passo-passo nel progetto. Grbl 0.9 compliant. (Open Firmware fonte in esecuzione su un UNO Arduino che converte il codice G comandi in segnali passo dopo passo)

Si noti che questo è un kit smontato e la necessità di saldare.

Nota: Quando si inserisce il A4988 modulo deve fare attenzione a non inserire in senso inverso. Cablaggio motore passo-passo come segue: 2A, 2B è un (rosso, verde), 1A, 1B
gruppo è un gruppo (blu, giallo), se si desidera cambiare direzione, è possibile modificare
la posizione di un gruppo, per esempio 2A, 2B reciprocamente scambiate.

Il pacchetto comprende: 1 x V3.0 CNC Shield per Arduino 1 x ONU R3 di Arduino Consiglio 4 x controller modulo con dissipatore di calore per Arduino A4988

Scopri di più

Gaoxing Tech. 5PCS A4988 Stepstick Stepper Motor Module Driver + dissipatore di calore per il 3D Reprap stampante (confezione da 5 pezzi) (https://www.amazon.it/Gaoxing-Tech-Stepstick-dissipatore-confezione/dp/B06WLLZVP7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)


Stepper Motor Nema17 1.2A 3.6V 1.8 Degree Router Mill Robot Reprap DIY CNC for Arduino

Description:

Step Angle(deg) 1.8 Motor Length(mm) 48 RatedVoltage(V) 3.6 Phase Current(A) 1.2 Phase Resistance(Ohm) 3 Phase Inductance(mH) 5 Holding Torque(N.m) 5 Lead Wire(No) 4 Motor Weight(kg) 0.35

Package Included:

5 x StepStick Stepper motor driver module A4988. 5 x Heatsinks with sticky base. Scopri di più

XCSOURCE Nema 17 2 Fase 4 fili motore passo-passo 1.8 gradi 42 x 42 x 34mm Per 3D stampante TE225 (https://www.amazon.it/XCSOURCE-motore-passo-passo-stampante-TE225/dp/B011NRMXYO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)

Descrizione:


Girare per: L'ordine del potere AB-BC-CD-DA, dal lato albero vedere CW Corrente nominale (monofase): 1.5A DC Tensione nominale: 3.45V Angolo di Stepping: 1.8 a

Specifiche tecniche:

Condizioni di esercizio: Ambiente Temperatura: -20 ~ 50 ; RH: 90% MAX; Posizione di montaggio: Asse installazione orizzontale o verticale A corrente continua la resistenza degli avvolgimenti (25): 2.3|10% Wnding induttanza: 3mH 20% Cogging: 12mN.m REF. Coppia di mantenimento: 300mN.m i = 1,5 Max. a vuoto frequenza di avviamento: 1500pps Max. a vuoto Frequenza esecuzione: 8000pps Aumento di temperatura: Passo Precisione angolo: 1.8a 5% L'inerzia rotante: 38g.cm2 Motore Peso: 0.23kg / PC RIF. Resistenza di isolamento: resistenza di isolamento freddo dovrebbe essere piu di 100m|? (tra il nucleo dello statore del motore e terminali) Rigiditša dielettrica: Lo spazio tra il nucleo dello statore del motore e terminale deve essere in grado di sopportare AC600V / 1s senza rompersi. La corrente di dispersione minore di 1 mA.

Il pacchetto include:

Stampante 2 Fase 4 fili 1 X Nema 17 3D motore passo a passo 1,8 per 17HD34008-22B 1 X cavo

Scopri di più


Motori Passo Passo Kuman K67 Per Arduino (5 set) - Motore Passo Passo 28BYJ-48 ULN2003 5V + Scheda Driver ULN2003 +Dupont Wire Cavo Jumper Maschio-Femmina 40 (https://www.amazon.it/Motori-Passo-Kuman-Arduino-Maschio-Femmina/dp/B01IP6RBJS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)


Pin

DESCRIPTION Caratteristiche: Dimensioni della scheda Drive(inch): 1.37x1.18x0.6; Diametro del motore passo passo: 1.06(inch); Linea del motore passo passo: 9.45(inch) A, B, C, D i LED delle quattro fasi indicano lo stato del motore passo passo. Con una interfaccia standard e un attacco diretto.. 5 linee 4 di fase possono essere utilizzate per il chip driver ULN2003 ordinario, connessione a 2 fasi, supporta la tavola sperimentale di sviluppo，con uso pratico e docking diretto Voltaggio nominale:DC5V 4-phase Resistenza di isolamento: >10MΩ (500V) Rigidità dielettrica: 600V AC / 1mA / 1s Angolo del passo: 5.625 x 1/64 Resistenza DC: 200Ω±7% (25C) Tasso di riduzione: 1/64 Grado di isolamento: A Frequenza tiraggio a vuoto: >600Hz Frequenza spinta a vuoto: >1000Hz Tiraggio di coppia: >34.3mN.m(120Hz) temperatura: 40K(120Hz)Contenuto della confezione: 5x Motore passo passo Uln2003 Driver Board*5 1x cavo jumper maschio-femmina 40-pin
Scopri di più

Hossen - Motore passo-passo NEMA 17 per fresatrice CNC, 57 oz-in 1 Nm, 1,3 A, 40 mm (https://www.amazon.it/Hossen-Motore-passo-passo-fresatrice-oz-/dp/B00CMJ4Y68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)


Scopri di più

Generico 28BYJ-48: Micro motore passo-passo DC 5V 4-fasi 5-fili con modulo di azionamento ULN2003 (https://www.amazon.it/Generico-28BYJ-48-passo-passo-azionamento-ULN2003/dp/B00DGNO6PI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)


Questo può 5 Scala 4 fasi motore passo passo attraverso la ULN2003 chip, con questo motore passo passo. Con filo e spina, può essere utilizzata direttamente questo motore passo passo con madre di sviluppo. Descrizione: Si tratta di un alta qualità motore passo passo Arriva con cavo e spina, facile da usare Arriva con un modulo driver ULN2003 A, B, C, D quattro fasi sull' unità modulo scheda LED indica lo stato del lavoro motore passo-passo Modello motore: 28byj 48 Tensione: 5 V DC Angolo di passo: 5.625 x 1/64 Reduction ratio: 1/64 Fase: 4 Diametro del motore: 28 mm circa. Lunghezza del cavo: circa 24 cm (collegare il connettore) Drive Module Board Dimensioni (l x w): circa 35 x 31 mm Contenuto della confezione: 1 x Motore Passo-passo 1 x aviazione modulo di ULN2003
Scopri di più


VORCOOL Nema 17 Motore Passo a Passo con Cavo per Stampante 3D
- 4 Fili Fase 2 34mm 1.8° (https://www.amazon.it/VORCOOL-Nema-Motore-Passo-Stampante/dp/B01B2C7JU8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)


Descrizione Questo articolo è un motore passo-passo, con cavo a 4 pin per un utilizzo conveniente, adatto per motori passo-passo tipo 17HD34008-22B. Necessario sostituzione della stampante 3D. Caratteristiche - Adatto per motori passo-passo tipo 17HD34008-22B. - Modalità di azionamento: Azionamento corrente a corrente continua. -Modalità eccitante: Due fasi a 4 fili, è disponibile per la rotazione di avanti e indietro. -Tornare a: L'ordine del potere è AB-BC-CD-DA, dall'estremità dell'albero vedi CW -corrente nominale (monofase): 1.2A DC. - Tensione nominale: 3.45V. - Angolo di avanzamento: 1,8 °. specificazioni - Temperatura ambiente: -20 ~ 50 ℃. - RH: 90% MAX - Resistenza all'avvolgimento della corrente diretta (25 ℃): 2,3Ω ± 10% - Induttanza di wnding: 3mH ± 20% - Cogging: 12mN.m REF. - coppia di serraggio: ≥300mN.m (I = 1,5A) - Max. Frequenza di avviamento senza carico: ≥1500pps - Max. Frequenza senza carico Frequenza: ≥8000pps - Aumento della temperatura: - precisione angolo passo: 1,8 ° ± 5% - Inerzia rotativa: 38g.cm2 - Peso motore: 0.23Kg / PC REF. - La corrente di dispersione è inferiore a 1 mA. - Formato (L * W * H): ca. 42 * 42 * 34mm / 1.65 * 1,65 * 1,34 pollici Pacchetto compreso 1 * Nema 17 2 Fase 4-Wire 1.5A 1.8 ° Motore passo-passo per stampante 3D 1 * cavo
Scopri di più

Arduino Uno Microcontrollore (https://www.amazon.it/ARDUINO-A000066-Arduino-Uno-Microcontrollore/dp/B008GRTSV6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)


Quizás quisiste decir: Éste nuevo Arduino UNO (Rev 3) es muy parecido a su predecesor Duemilanove siendo totalmente compatible. Este modelo de Arduino UNO realiza una selección de voltaje de alimentación automática (DC/USB) mediante un chip MOSFET incluido en la placa. Incorpora un nuevo bootloader que nos posibilita cargar programas a 115Kbps. El bootloader ahora ocupa menos (512bytes) gracias a una conseguida reducción de tamaño, por lo que tendremos más espacio para nuestra programación. Incluye: Placa Arduino UNO rev.3 Questa nuova UNO Arduino (Rev3) è molto simile al suo predecessore Duemilanove è pienamente compatibile. Questo modello di ONU di Arduino fa una selezione di tensione automatica (DC / USB) tramite una piastra contenuta nel chip MOSFET. Incorpora un nuovo bootloader che ci permette di caricare programmi a 115Kbps. Il bootloader ora occupa meno (512 byte) realizzati attraverso una riduzione delle dimensioni, in modo da avere più spazio per la nostra programmazione. Esso include: ONU di Arduino rev.3
Scopri di più

Elegoo UNO R3 Board Scheda ATmega328P ATMEGA16U2 con Cavo USB Compatibile con Arduino UNO R3 Microcontrollore (https://www.amazon.it/Elegoo-ATmega328P-ATMEGA16U2-Compatibile-Microcontrollore/dp/B01MRJR8UF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)


Noi abbiamo la fabbrica di produzione, Produciamo e vendiamo i nostri prodotti. Quindi controlliamo noi stessi la qualità dei prodotti per te. Vorremmo ricevere i vostri preziosi suggerimenti per trasformare le vostre idee in realtà. Caratteristiche: * ATmega328P microcontroller * Tensione d'ingresso - 7-12V * 5V corrente: 500 mA * 3.3V corrente: 50 mA * 14 Pin Digital I/O (6 uscite PWM ) * 8 ingressi analogici * 32k memoria flash * 16Mhz velocità del clock.Elenco dei componenti: 1 pezzo UNO R3 Microcontrollore 1 pezzo Cavo USB
Scopri di più

Elegoo Progetto Arduino Scheda UNO R3 Starter Kit Super per Principianti con Tutorial in Italiano Learing Kit di Apprendimento (https://www.amazon.it/Elegoo-Progetto-Principianti-Tutorial-Apprendimento/dp/B01N921CM2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)

Elegoo Inc. è un produttore ed esportatore professionale che si occupa di progettazione, produzione sviluppo e commercializzazione di arduino, stampanti 3D, Raspberry Pi e STM32. Il nostro sogno è quello di fare il miglior prezzo e la migliore qualità dei prodotti per i clienti. Quindi vorremmo ricevere i vostri preziosi suggerimenti per trasformare le vostre idee in realtà.Avvertimento: La tensione di ingresso Elegoo modulo di alimentazione è 6.5V - 9v (DC). Si prega di NON superarla, altrimenti si brucerà la vostra board. Elegoo Progetto Super Starter Kit per ArduinoLista componenti: 1pcs UNO R3 scheda 1pcs LCD1602 Modulo (con connettori pin) 1pcs Breadboard espansione 1pcs Modulo alimentazione 1pcs Joystick Modulo 1pcs IR Ricevitore 1pcs Servo Motore (SG90) 1pcs Stepper Motore 1pcs ULN2003 Stepper Motor Driver Board 1pcs Sensor a ultrasuoni 1pcs DHT11 Modulo temperature e umidità 1pcs 9V Batteria with DC 1pcs 65 Jumper cavetti 1pcs USB Cavo 1pcs Cicalino attivo 1pcs Cicalino passivo 1pcs Potenziometro 1pcs 5V Relay 1pcs Breadboard 1pcs Remoto 1pcs Tilt Switch 5pcs Bottone (piccolo) 1pcs 1 digit 7-segment Display 1pcs 4 digit 7-segment Display 5pcs Giallo LED 5pcs Blu LED 5pcs Verde LED 5pcs Rosso LED 1pcs RGB LED 2pcs Fotoresistenza 1pcs Termistore 2pcs Diode Raddrizzatore (1N4007) 2pcs NPN Transistor (PN2222) 1pcs IC 74HC595 10pcs Resistenze (10 Ω) 10pcs Resistenze (100 Ω) 30pcs Resistenze (220 Ω) 10pcs Resistenze (330 Ω) 10pcs Resistenze (1K Ω) 10pcs Resistenze (2K Ω) 10pcs Resistenze (5.1K Ω) 10pcs Resistenze (10K Ω) 10pcs Resistenze (100K Ω) 10pcs Resistenze (1M Ω) 10pcs Cavetti jumper da Femmina a Maschio 1pcs CD con tutorial in Italiano
Scopri di più

tinxi® Nuova Versione R3 ATmega328P CH340 per Arduino + USB Cavo (https://www.amazon.it/tinxi%C2%AE-Nuova-Versione-ATmega328P-Arduino/dp/B01C2Q0NNS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)


Add two rows of the holes for the pins. So it can be connected with normal Dubond line. Add 3 rows of the holes for wiring. Change the in-line package of ATMEGA328P to flat package. CH340G Replace ATmega16U2 Plug UNO development board, the driver will be automatically installed. select the board UNO inside the die. Select the COM port, this can be in my computer queries, just inside your uno port development board You'd better to choose arduino own routine procedures, burn into the board.

Confezione: 1x ATmega328P Board 1x USB Cavo

Scopri di più

tinxi® ATMEGA16U2 Versione Uno R3 MEGA328P Board con USB cavo compatibile con Arduino (https://www.amazon.it/ATMEGA16U2-Versione-MEGA328P-compatibile-Arduino/dp/B01C2NTQ2K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)

Arduino Uno Rev3 è una scheda elettronica basata sul microcontrollore Atmega328. Dispone di 14 ingressi/uscite digitali (di cui 6 possono essere utilizzate come uscite PWM), 6 ingressi analogici, un cristallo oscillatore a 16 MHz, una connessione USB, un jack di alimentazione, un header ICSP e un pulsante di reset. Contiene tutto il necessario per supportare il microcontrollore; per iniziare basta connettersi a un computer tramite un cavo USB o alimentarla con un trasformatore AC/DC o una batteria. La UNO si differenzia da tutte le schede precedenti in quanto non utilizza il convertitore USB-seriale FTDI ma un microcontrollere Atmega16U2 programmato come un convertitore USB-seriale. Microcontrollore: ATmega328 Tensione operativa: 5 V Alimentazione: - da 7 a 12 V (tramite plug) - 5 V (tramite porta USB) Tensione di alimentazione (limiti): 6-20V Ingressi/uscite Digitali: 14 (di cui 6 possono essere utilizzate come uscite PWM) Ingressi analogici: 6 Corrente Dc per pin I/O: 40 mA Corrente DC per pin 3,3 V: 50 mA Memoria Flash: 32 kB (di cui 0,5 kB utilizzati dal bootloader) SRAM: 2 kB EEPROM: 1 kB Velocità di Clock : 16 MHz

Confezione: 1 * Arduino Board 1 * USB Cavo

Scopri di più

PsmGoods 12 valore 120 pz condensatori elettrolitici kit 50V1UF, 50V2.2UF, 50V3.3UF, 50V4.7UF, 50V10UF, 25V22UF, 25V33UF, 25V47UF, 16V100UF, 16V220UF, 16V330UF, 16V470UF (https://www.amazon.it/PsmGoods-condensatori-elettrolitici-50V2-2UF-50V3-3UF/dp/B00XBI4JJQ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)


Scopri di più

Aussel 24 Valore 500 Pezzi Kit elettrolitico Kit Assortimento Kit Kit Kit 0.1uF-1000uF (https://www.amazon.it/Aussel-Valore-elettrolitico-Assortimento-0-1uF-1000uF/dp/B01MXSF7YT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)

Alta qualità e lunga durata. Capacità nominale: 0.1uF ~ 1000uF Tolleranza di capacità: elettrolitico +/- 20% Gamma di temperatura di funzionamento: -40deg / C ~ 105 + deg / C Coefficiente di temperatura: da -55 a + 175deg CElenco dei pacchetti: 0.1uF 50V 4x7 30 pezzi 0.22uF 50V 5x11 20 pezzi 0.47uF 50V 5x11 20 pezzi 1uF 50V 5x11 20 pezzi 2.2uF 50V 4x7 30 pezzi 3.3uF 50V 4x7 30 pezzi 4.7uF 50V 4x7 30 pezzi 10uF 25V 4x7 30 pezzi 10uF 50V 5x11 20 pezzi 22uF 16V 4x7 30 pezzi 22uF 25V 4x7 30 pezzi 33uF 16V 4x7 30 pezzi 47uF 10V 4x7 30 pezzi 47uF 25V 5x11 20 pezzi 47uF 50V 6x11 15 pezzi 100uF 16V 5x11 20 pezzi 100uF 25V 5x11 15 pezzi 220uF 10V 5x11 15 pezzi 220uF 25V 6x11 15 pezzi 330uF 25V 8x12 10 pezzi 470uF 10V 6x11 10 pezzi 470uF 16V 8x12 10 pezzi 680uF 16V 8x12 10 pezzi 1000uF 16V 10x16 10 pezzi

Scopri di più

Aerzetix - Condensatore elettrolitico , chimico , 6800µF ± 20% 25V THT 85°C 2000h Ø18x35.5mm radiale . (https://www.amazon.it/Aerzetix-Condensatore-elettrolitico-chimico-%C3%9818x35-5mm/dp/B01LVWTAHJ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)


Condensatore elettrolitico , chimico , 6800µF ± 20% 25V THT 85°C 2000h Ø18x35.5mm radiale .SK2-C12776-C342
Scopri di più

Tinksky 125pcs 25 valori totale condensatori elettrolitici assortimento Kit impostato 1uF 2200uF (https://www.amazon.it/Tinksky-condensatori-elettrolitici-assortimento-impostato/dp/B01A6OQ1IO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)

Caratteristiche-125 pezzi dei 25 condensatori elettrolitici valori in un set saranno venduti insieme.-Colore: il nero principalmente.-Materiale: metallo durevole.-Codice marker su ogni condensatore.-Quantità: 25 valori x 5pcs, 125pcs in totale:16V/47uF 16V/100uF 16V/220uF, 470uF/16V, 16V/1000uF;25V/10uF 25V/47uF, 25V/100uF, 25V/220uF, 25V/330uF, 25V/470uF, 25V/1000uF, 25V/2200uF;50V/1uF, 50V / 3.3 UF, 50V / 4.7 UF, 50V / 6.8 UF, 50V/10uF 50V/33uF 50V/47uF, 50V/100uF, 50V/220uF, 50V/330uF, 50V/470V, 50V/1000uF.Pacchetto che comprende1 * set di 125pcs 25 valori totali 1uF condensatori elettrolitici a 2200uF (nero)
Scopri di più

Sourcingmap - 30pcs 35v 100uf piombo radiale condensatore elettrolitico 6 millimetri x 12mm (https://www.amazon.it/Sourcingmap-radiale-condensatore-elettrolitico-millimetri/dp/B00JR3XKEE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)

(1) (https://www.amazon.it/product-reviews/B00JR3XKEE?showViewpoints=1)
Specification:Product NameElectrolytic CapacitorTypeRadialTemperature Range-40+105CVoltage35VCapacitance100uFBody Size6mm x 12mm/ 0.24" x 0.47"(D*H)Lead Space2mmLead Length19mm, 24mmTotal Weight18gMain ColorBlackPackage Content30 x Electrolytic CapacitorsDescription:Perfect for Computer Motherboard.Polarized, longer lead is positive while the other lead is negative.Radial design.
Scopri di più

Il video

Ricerche che hanno riportato a questa pagina:

schema 4motori passo passo e comanda (https://www.lombardoandrea.com/motori-passo-passo-arduino-joystick/) (3) arduino accelstepper (https://www.lombardoandrea.com/motori-passo-passo-arduino-joystick/) (1)
arduino ir con joistick (https://www.lombardoandrea.com/motori-passo-passo-arduino-joystick/) (1)
controllo xy motore stepper (https://www.lombardoandrea.com/motori-passo-passo-arduino-joystick/) (1)
tobot a 4 assi con arduino (https://www.lombardoandrea.com/motori-passo-passo-arduino-joystick/) (1)

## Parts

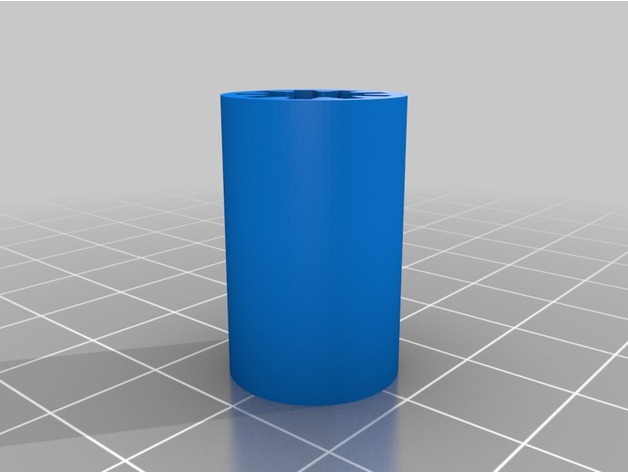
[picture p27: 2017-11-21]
Documenti_Esterni/Evo_Parts/images/BOCCOLA.jpg

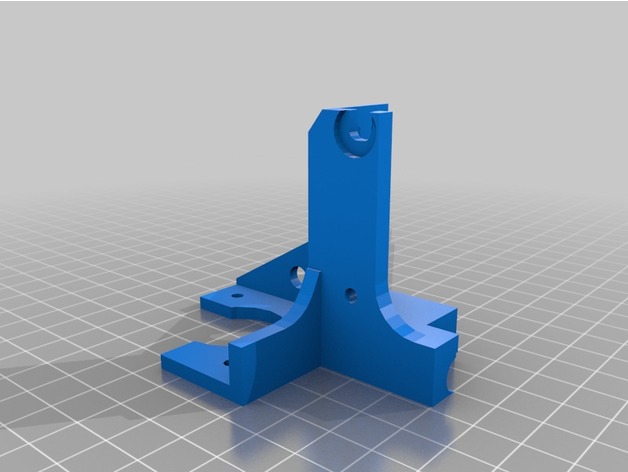
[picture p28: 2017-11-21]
Documenti_Esterni/Evo_Parts/images/GONDOLA_MOTORE_DESTRA.jpg

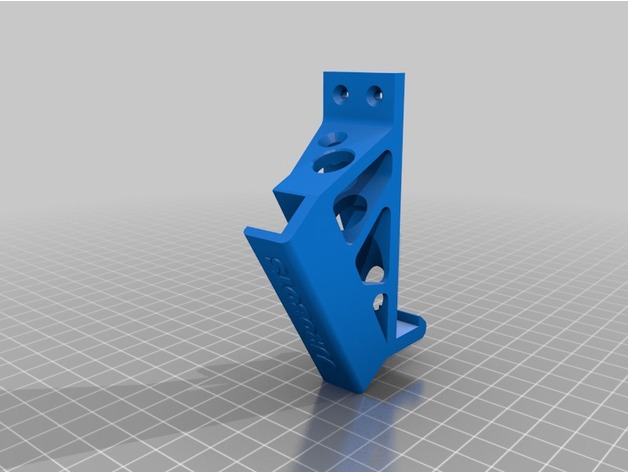
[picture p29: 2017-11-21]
Documenti_Esterni/Evo_Parts/images/BASE_SUPPORTO_ASTA.jpg

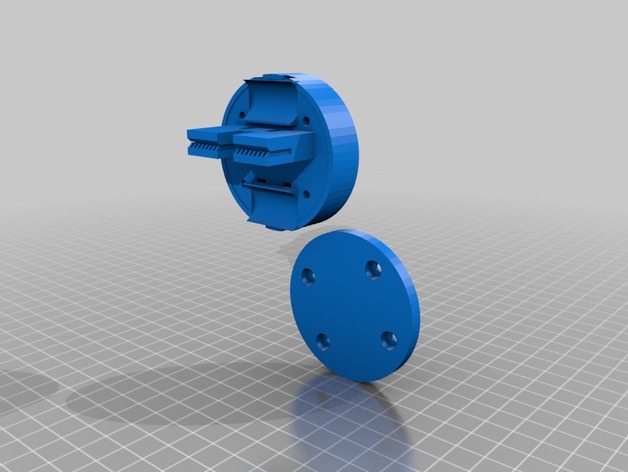
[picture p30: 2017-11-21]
Documenti_Esterni/Evo_Parts/images/PUSHER_2PARTI.jpg

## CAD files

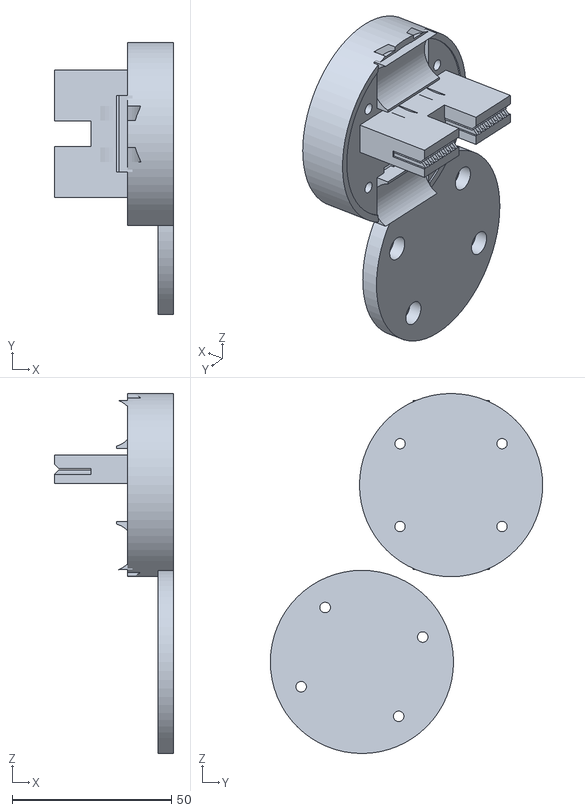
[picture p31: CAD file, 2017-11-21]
Documenti_Esterni/Evo_Parts/files/PUSHER_2PARTI.stl
37.5 x 85.5 x 113.0

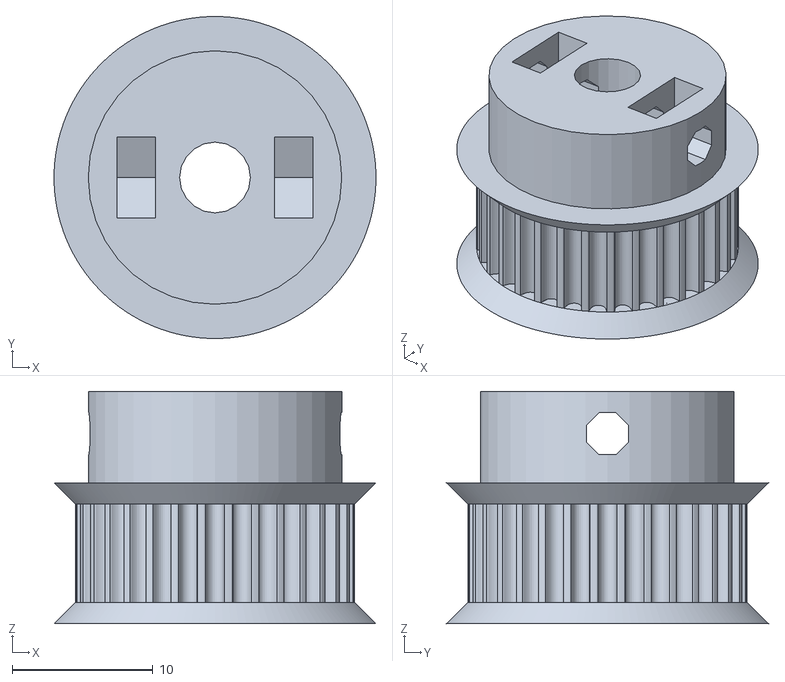
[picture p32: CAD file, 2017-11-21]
Documenti_Esterni/Evo_Parts/files/PULEGGIA_MOTORE.stl
22.9 x 22.9 x 16.5

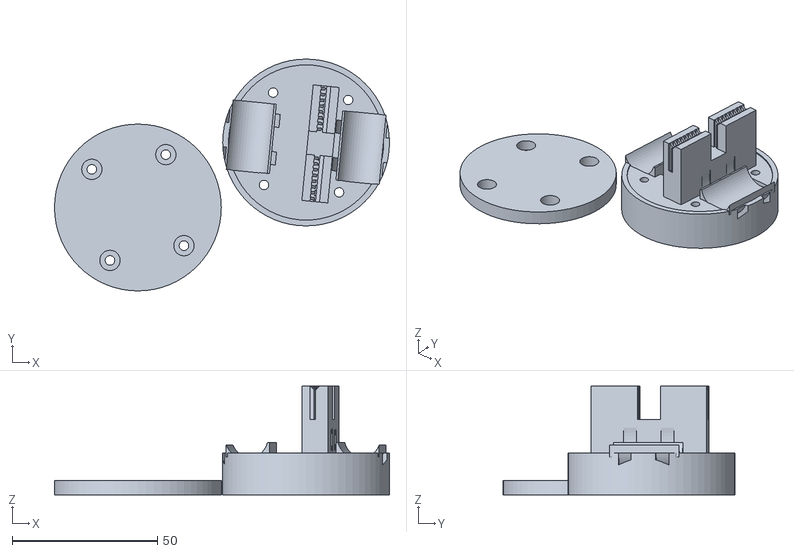
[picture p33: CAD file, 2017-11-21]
Documenti_Esterni/Evo_Parts/files/PAW_PUSHER_2PARTI_90°.stl
115.5 x 79.9 x 37.5

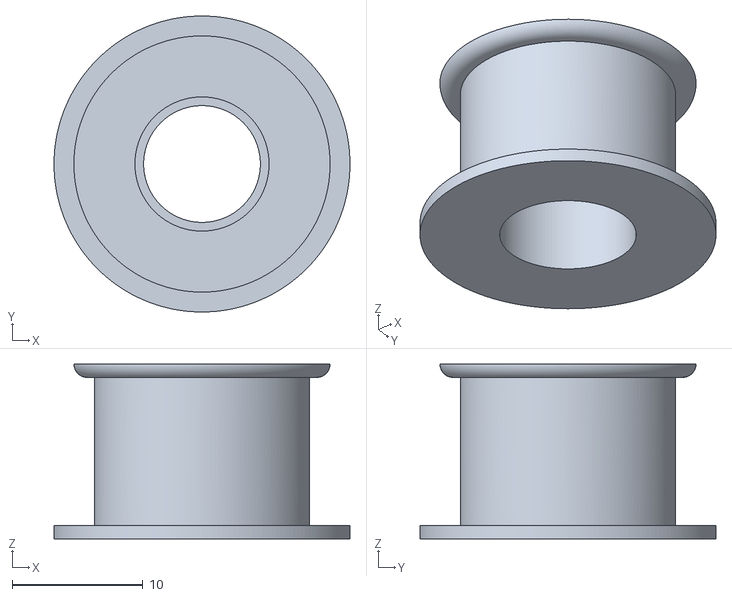
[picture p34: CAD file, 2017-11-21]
Documenti_Esterni/Evo_Parts/files/623_PULEGGIA_LIBERA.stl
22.7 x 22.7 x 13.4

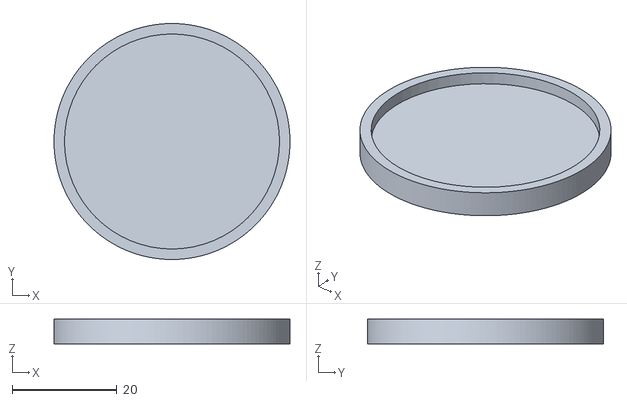
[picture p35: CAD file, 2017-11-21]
Documenti_Esterni/Evo_Parts/files/PUCK.stl
45.0 x 45.0 x 4.75

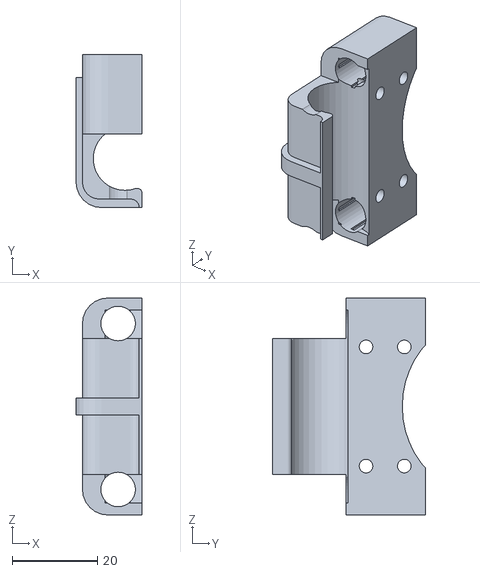
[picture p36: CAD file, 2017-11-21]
Documenti_Esterni/Evo_Parts/files/CURSORE_LATERALE.stl
15.5 x 36.0 x 51.0

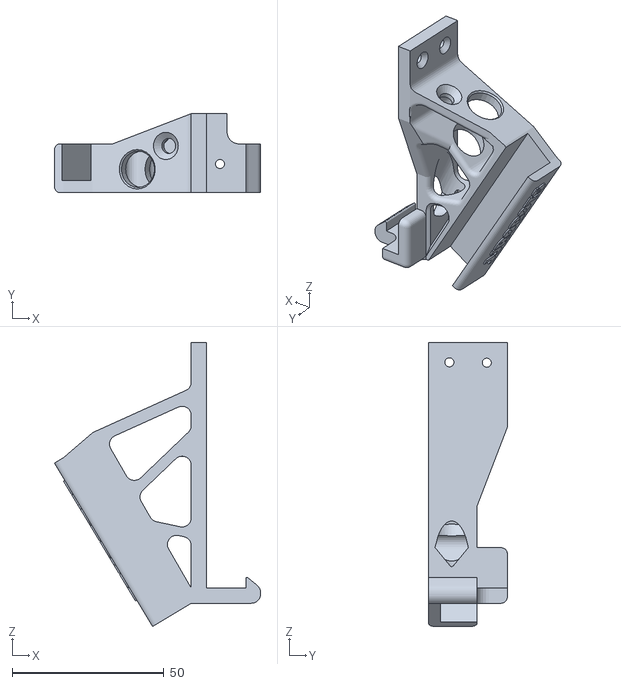
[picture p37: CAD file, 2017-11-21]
Documenti_Esterni/Evo_Parts/files/BASE_SUPPORTO_ASTA.stl
68.0 x 26.0 x 93.7

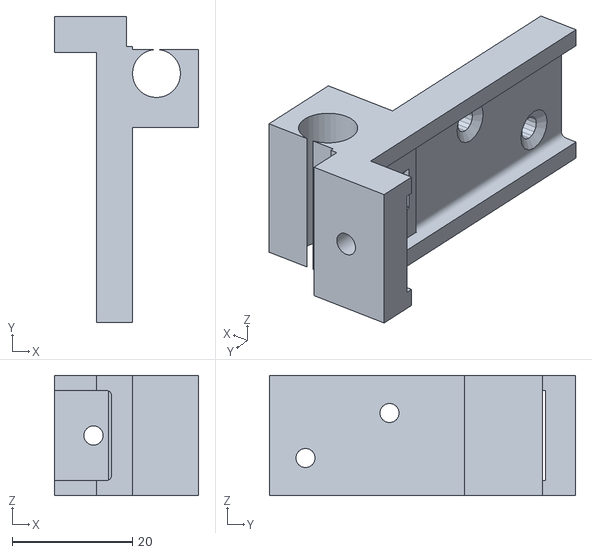
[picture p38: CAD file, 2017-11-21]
Documenti_Esterni/Evo_Parts/files/SUPPORTO_LATERALE.stl
24.0 x 51.0 x 20.0

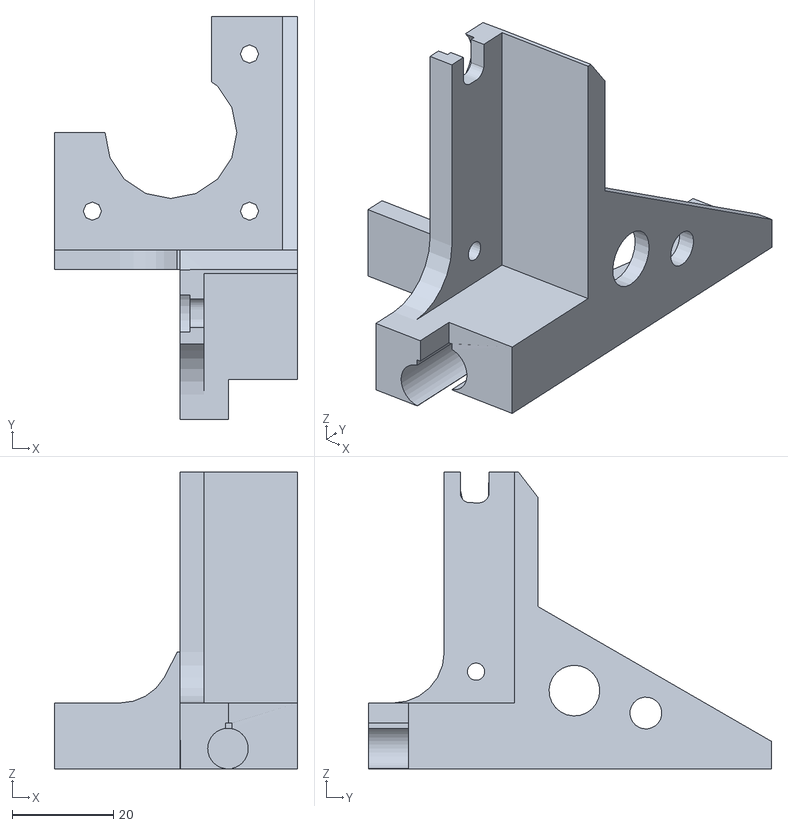
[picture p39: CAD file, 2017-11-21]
Documenti_Esterni/Evo_Parts/files/GONDOLA_MOTORE_DESTRA.stl
48.0 x 79.5 x 58.5

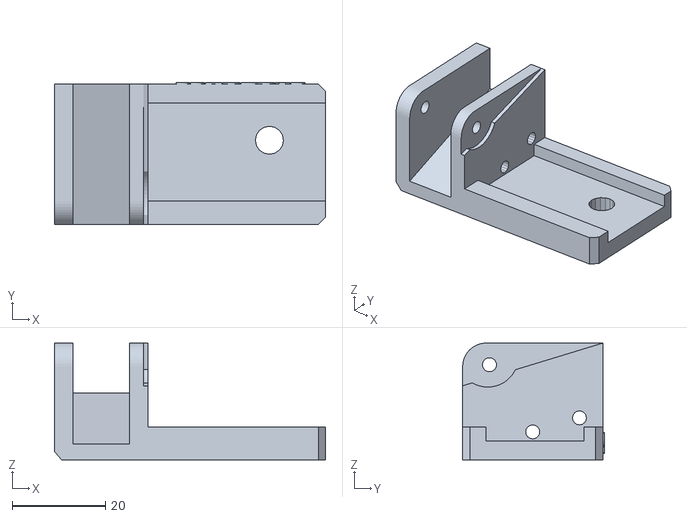
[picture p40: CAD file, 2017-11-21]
Documenti_Esterni/Evo_Parts/files/SUPPORTO_SMARTPHONE_SUPERIORE.stl
58.0 x 30.3 x 25.0

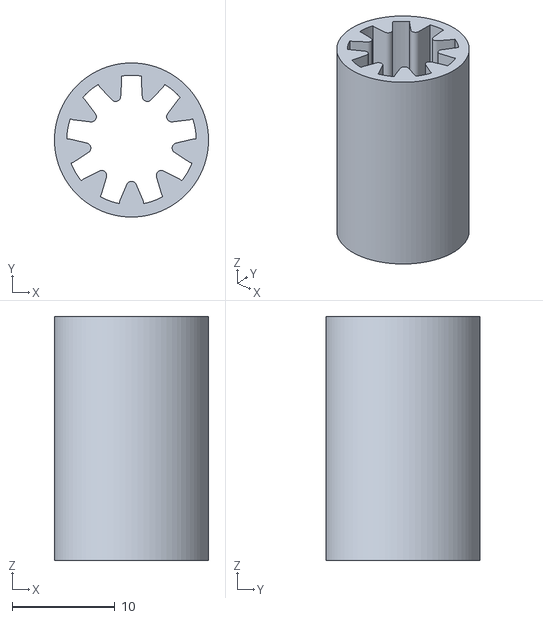
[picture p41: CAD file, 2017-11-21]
Documenti_Esterni/Evo_Parts/files/BOCCOLA.stl
15.0 x 15.0 x 23.8

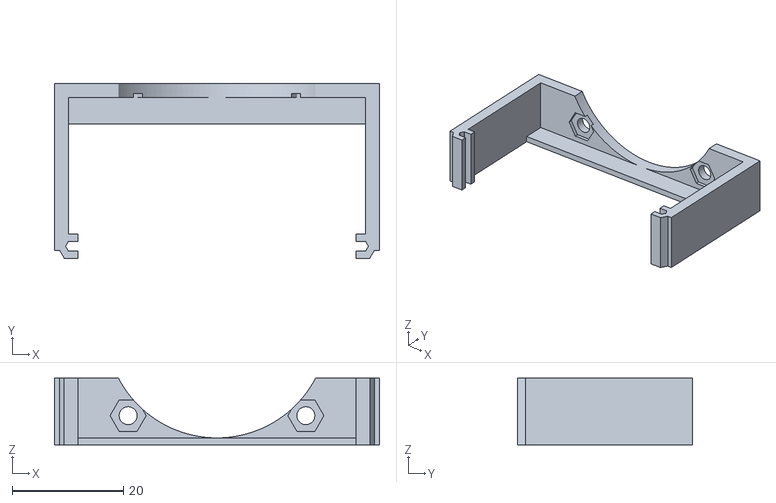
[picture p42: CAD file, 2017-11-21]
Documenti_Esterni/Evo_Parts/files/SUPPORTO_VENTOLA.stl
58.5 x 31.4 x 12.0

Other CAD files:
Documenti_Esterni/Evo_Parts/files/GONDOLA_MOTORE_SINISTRA.stl

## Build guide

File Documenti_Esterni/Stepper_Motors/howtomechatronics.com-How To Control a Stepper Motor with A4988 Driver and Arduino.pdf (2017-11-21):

Dejan
Nedelkovski

16/8/2015

# How To Control a Stepper Motor with A4988 Driver and Arduino

howtomechatronics.com /tutorials/arduino/how-to-control-stepper-motor-with-a4988-driver-and-arduino/ (http://howtomechatronics.com/tutorials/arduino/how-to-control-stepper-motor-with-a4988-driver-and-arduino/)

In this Arduino Tutorial we will learn how to control a Stepper Motor (http://howtomechatronics.com/how-it-works/electrical-engineering/stepper-motor/) using the A4988 Stepper Driver. You can watch the following video or read the written tutorial below.

Overview

The A4988 is a microstepping driver for controlling bipolar stepper motors which has built-in translator for easy operation. This means that we can control the stepper motor with just 2 pins from our controller, or one for controlling the rotation direction and the other for controlling the steps.

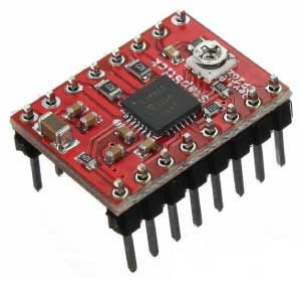
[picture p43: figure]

The Driver provides five different step resolutions: full-step, haft-step,
quarter-step, eight-step and sixteenth-step. Also, it has a potentiometer for
adjusting the current output, over-temperature thermal shutdown and crossover-current protection.

Its logic voltage is from 3 to 5.5 V and the maximum current per phase is 2A if good addition cooling is provided or 1A continuous current per phase without heat sink or cooling.

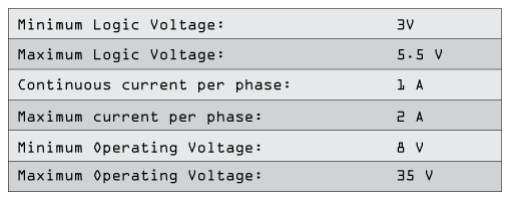
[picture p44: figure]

### A4988 Stepper Driver Pinout

Now let’s close look at the pinout of the driver and hook it up with the stepper motor and the controller. So we will start with the 2 pins on the button right side for powering the driver, the VDD and Ground pins that we need to connect them to a power supply of 3 to 5.5 V and in our case that will be our controller, the Arduino Board which will provide 5 V. The following 4 pins are for connecting the motor. The 1A and 1B pins will be connected to one coil of the motor and the 2A and 2B pins to the other coil of the motor. For powering the motor we use the next 2 pins, Ground and VMOT that we need to connect them to Power Supply from 8 to 35 V and also we need to use decoupling capacitor with at least 47 µF for protecting the driver board from voltage spikes.

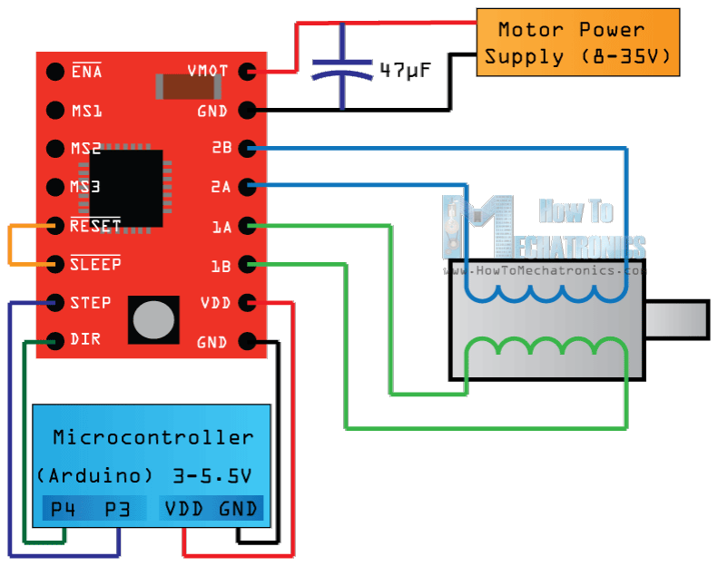
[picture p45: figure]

The next two 2 pins, Step and Direction are the pins that we actually use for controlling the motor movements. The Direction pin controls the rotation direction of the motor and we need to connect it to one of the digital pins on our microcontroller, or in our case I will connect it to the pin number 4 of my Arduino Board. With the Step pin we control the mirosteps of the motor and with each pulse sent to this pin the motor moves one step. So that means that we don’t need any complex programming, phase sequence tables, frequency control lines and so on, because the built-in translator of the A4988 Driver takes care of everything. Here we also need to mention that these 2 pins are not pulled to any voltage internally, so we should not leave them floating in our program.

Next is the SLEEP Pin and a logic low puts the board in sleep mode for minimizing power consumption when the motor is not in use.

Next, the RESET pin sets the translator to a predefined Home state. This Home state or Home Microstep Position can be seen from these Figures from the A4988 Datasheet. So these are the initial positions from where the motor starts and they are different depending on the microstep resolution. If the input state to this pin is a logic low all the STEP inputs will be ignored. The Reset pin is a floating pin so if we don’t have intention of controlling it with in our program we need to connect it to the SLEEP pin in order to bring it high and enable the board.

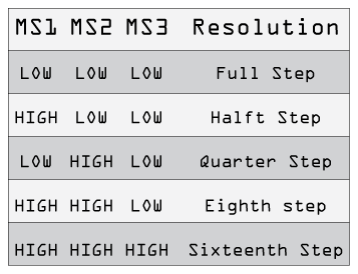
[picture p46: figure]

The next 3 pins (MS1, MS2 and MS3) are for selecting one of the five step resolutions according to the above truth table. These pins have internal pull-down resistors so if we leave them disconnected, the board will operate in full step mode.

The last one, the ENABLE pin is used for turning on or off the FET outputs. So a logic high will keep the outputs disabled.

### Components needed for this Arduino Tutorial

You can get the components from any of the sites below:

Stepper Motor (NEMA17) | Amazon (http://howtomechatronics.com/recommends/stepper-motor-amazon/) / Banggood (http://howtomechatronics.com/recommends/nema17-two-phase-hybrid-stepper-motor/) / GearBest (http://howtomechatronics.com/recommends/stepper-motor-gearbest/) / DealExtreme (http://howtomechatronics.com/recommends/stepper-motor-dealextreme/) / ICStation (http://howtomechatronics.com/recommends/stepper-motor-icstation/)
A4988 Stepper Driver | Amazon (http://howtomechatronics.com/recommends/a4988-driver-amazon/) / Banggood (http://howtomechatronics.com/recommends/a4988-reprap-step-motor-driver-module-bg/) / GearBest (http://howtomechatronics.com/recommends/a4988-driver-gearbest/) / DealExtreme (http://howtomechatronics.com/recommends/a4988-driver-dealextreme/) / ICStation (http://howtomechatronics.com/recommends/a4988-driver-icstation/)
12V 2AAdapter | Amazon (http://howtomechatronics.com/recommends/adapter-12v-2a-amazon/) / Banggood (http://howtomechatronics.com/recommends/12v-2a-adapter-bg/) / GearBest (http://howtomechatronics.com/recommends/adapter-12v-2a-gearbest/) / DealExtreme (http://howtomechatronics.com/recommends/adapter-12v-2a-dealextreme/)
Power Jack | Amazon (http://howtomechatronics.com/recommends/power-jack-amazon/) / Bangood (http://howtomechatronics.com/recommends/5-5mm-x-2-1mm-dc-power-jack-socket-bg/) / DealExtreme (http://howtomechatronics.com/recommends/power-jack-dealextreme/)
Arduino Board | Amazon (http://howtomechatronics.com/recommends/arduino-mega-board-amazon/) / Banggood (http://howtomechatronics.com/recommends/arduino-mega-board/) / GearBest (http://howtomechatronics.com/recommends/arduino-mega-board-gearbest/) / DealExtreme (http://howtomechatronics.com/recommends/arduino-mega-board-dealextreme/) / ICStation (http://howtomechatronics.com/recommends/arduino-mega-2560-board-ic/)
Breadboard and Jump wires… Amazon (http://howtomechatronics.com/recommends/breadboard-jumper-wires-kit-amazon/) / Banggood (http://howtomechatronics.com/recommends/solderless-pcb-breadboard-jump-wires-bg/) / GearBest (http://howtomechatronics.com/recommends/breadboard-jump-wires-gearbest/) / DealExtreme (http://howtomechatronics.com/recommends/breadboard-kit-dealextreme/) / ICStation (http://howtomechatronics.com/recommends/breadboard-jump-wires-ic/)

*Please note: These are affiliate links. I may make a commission if you buy the components through these links. I would appreciate your support in this way!

### Circuit Schematics

Here’s the complete circuit schematics. I will use the drive in Full Step Mode so I will leave the 3 MS pins disconnected and just connect the Direction and the Step pins of the drive to the pins number 3 and 4 on the Arduino Board and as well the Ground and the 5 V pins for powering the board. Also I will use a 100µF capacitor for decoupling and 12V, 1.5A adapter for powering the motor. I will use a NEMA 17 bipolar Stepper Motor and its wires A and C will be connected to the pins 1A and 1B and the B and D wires to the 2A and 2B pins.

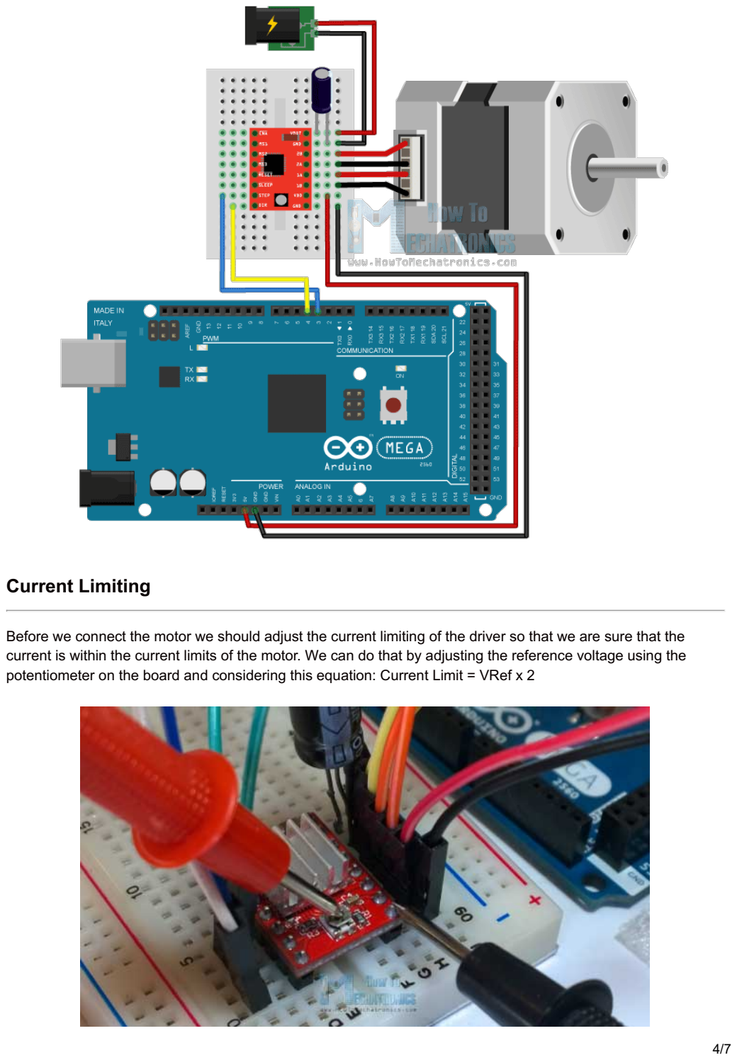
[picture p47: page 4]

### Current Limiting

Before we connect the motor we should adjust the current limiting of the driver so that we are sure that the current is within the current limits of the motor. We can do that by adjusting the reference voltage using the potentiometer on the board and considering this equation: Current Limit = VRef x 2

However this equation is not always correct as there are different manufactures of the A4988 driver board. Here’s a demonstration of my case: I adjusted the potentiometer and measured 0.6V reference voltage. So the current limiting should be that value of 0.6*2, equal 1.2 A.

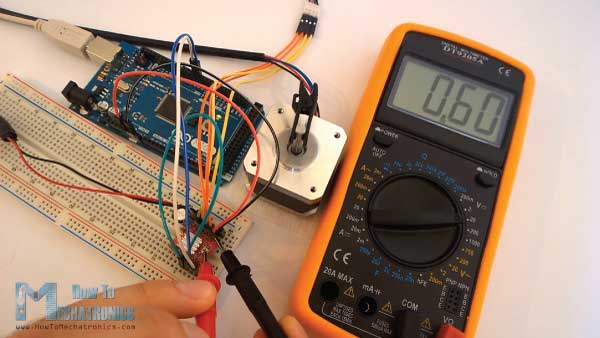
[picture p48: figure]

Now because I am using the Driver in Full Step Mode and according to the A4988 Datasheet in this mode the winding current could reach only 70% of the current limit, the 1.2A*0.7 would equal 0.84A. In order to check this I uploaded a simple code that sends continuous logic high to the Step pin (so that we can better notice the current) and connected my meter in series with one winding of the motor and powered it up. What I got was 0.5A which means that the equation wasn’t correct for my case.

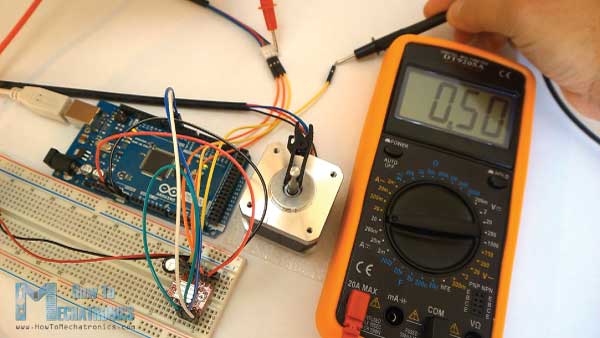
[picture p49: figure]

### Source Code

Here’s an example code. First we have to define the Step and Direction pins. In our case they are the pins number 3 and 4 on the Arduino Board and they are named stepPin and dirPin and the setup section we have to
define them as an outputs. | 5/7

1. /* Simple Stepper Motor Control Exaple Code
2. *
3. * by Dejan Nedelkovski, www.HowToMechatronics.com
4. *
5. */
6. // defines pins numbers
7. const int stepPin = 3;
8. const int dirPin = 4;
9. void setup() {
10. // Sets the two pins as Outputs
11. pinMode(stepPin,OUTPUT);
12. pinMode(dirPin,OUTPUT);
13. }
14. void loop() {
15. digitalWrite(dirPin,HIGH); // Enables the motor to move in a particular direction
16. // Makes 200 pulses for making one full cycle rotation
17. for(int x = 0; x < 200; x++) {
18. digitalWrite(stepPin,HIGH);
19. delayMicroseconds(500);
20. digitalWrite(stepPin,LOW);
21. delayMicroseconds(500);
22. }
23. delay(1000); // One second delay
24. digitalWrite(dirPin,LOW); //Changes the rotations direction
25. // Makes 400 pulses for making two full cycle rotation
26. for(int x = 0; x < 400; x++) {
27. digitalWrite(stepPin,HIGH);
28. delayMicroseconds(500);
29. digitalWrite(stepPin,LOW);
30. delayMicroseconds(500);
31. }
32. delay(1000);
33. }

In the loop section first we will set the Direction pin on high state that will enable the motor to move in a particular direction. Now using this for loop we will make the motor make one full cycle rotation. As the driver is set on Full Step Mode and our Stepper Motor has 1.8 degrees step angle, or 200 steps, we need to send 200 pulses into the Step Pin to make one full cycle rotation. So the for loop will have 200 iterations and each time it will set the Step pin on high and then low state for making the pulses. Between each digitalWrite we need add some delay from which the speed of the motor will depend.

After this full cycle rotation we will make one second delay, then change the direction of rotation by setting the dirPin on a low state and now make 2 full cycle rotations with this loop of 400 iterations. At the end there is one more second delay. Now let’s upload the code and see how it will work.

I made one more example for this tutorial, where I control the speed of the motor using a potentiometer. Here’s the source code of that example:

1. /* Simple Stepper Motor Control Exaple Code
2. *
3. * by Dejan Nedelkovski, www.HowToMechatronics.com
4. *
5. */
6. // Defines pins numbers
7. const int stepPin = 3;
8. const int dirPin = 4;
9. int customDelay,customDelayMapped; // Defines variables
10. void setup() {
11. // Sets the two pins as Outputs
12. pinMode(stepPin,OUTPUT);
13. pinMode(dirPin,OUTPUT);
14. digitalWrite(dirPin,HIGH); //Enables the motor to move in a particular direction
15. }
16. void loop() {
17. customDelayMapped = speedUp(); // Gets custom delay values from the custom speedUp function
18. // Makes pules with custom delay, depending on the Potentiometer, from which the speed of the motor depends
19. digitalWrite(stepPin, HIGH);
20. delayMicroseconds(customDelayMapped);
21. digitalWrite(stepPin, LOW);
22. delayMicroseconds(customDelayMapped);
23. }
24. // Function for reading the Potentiometer
25. int speedUp() {
26. int customDelay = analogRead(A0); // Reads the potentiometer
27. int newCustom = map(customDelay, 0, 1023, 300,4000); // Convrests the read values of the potentiometer from 0 to 1023 into desireded delay values (300 to 4000)
28. return newCustom;
29. }

JLCPCB: Prototype 10 PCBs for $2 (2-layer,100*100mm)

China's Largest PCB Prototype Manufacturer, 290,000+ Customers & 8,000+ Online Orders Per Day (https://jlcpcb.com/)

PCB Pricing: https://jlcpcb.com/quote

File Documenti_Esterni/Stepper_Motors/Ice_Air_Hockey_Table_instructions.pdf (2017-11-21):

# AIR HOCKEY ROBOT (AHRobot) BUILD INSTRUCTIONS

Project Blog:
Code Repository & Parts:
Other places of interest:
Licence:
Author: Jose Julio
Contributors:
(*) If you collaborate on the project, add your name to the list

Bill of materials (BOM).

This document is divided in the air hockey table and the robot.
AIR | HOCKEY | TABLE
- Wood thread screws
50 2.5x16mm
50 3x30mm
20 3x20mm

-Metric thread screws
16 M3x6mm
8 M3x12mm
24 M3 washers
16 M3 nuts
2 M3x20mm
8 M4x12mm
8 M4 nuts
- Wood boards
2 100x60cm x2.5mm MDF (white finish on one side)
- Solid wood slats (*)
2 44x18mm x 1m
3 44x18mmx56.4cm
2 12x18x 90cm (can be 12x12)
4-12x18x 12 cm
4 12x18x 6 cm
(*) if you don´t find the exact dimensions you can easily adapt the whole project ...
- hot glue gun
- EVA foam
- Drill and drill bits 1mm and 1.5mm

- Jigsaw (or marquetry saw) to open fan holes
- 2 90mm fans 12V 0.5A (you can also use 120mm size). This are typical PC fans (Important! 0.5A minimum, 0.6 or 0.8A better). I use old fans from PC power supplies.
- Cable and connectors for fans
AIR | HOCKEY | ROBOT

Typical RepRap 3D printer equipment:
- Arduino Mega 2560
- RAMPS 1.4
- 3 A4988 Drivers with heatsinks (or DRV8825)
- 12v fan ( Recommended 5-6cm) for electronics cooling
- 3 NEMA17 stepper motors 48N-cm (70oz-inch)
- Motor cable and connectors.
- Five meters of GT2 belt (or T5 belt)
- 2 8mm Stainless Steel rods 46cm (1 meter steel rod and cut)
- 2 8x1mm 65cm carbon tubes (kite tubes, easy to cut)
(can be replaced by aluminum tube 8x1mm)
UPDATED: New tube size!
- 1 8x1mm 87.5cm carbon tube (kite tube) for camera (can be replaced by aluminum tube 8x1mm)
- 3 608 bearings
- 3(or 4) LM8UU linear bearings
- Small nylon tag fasteners
- Set of 3D printed parts in PLA (repository)
- PS3 EYE Camera
- PC or laptop (i3 processor or higher recommended)
(In future, PC and PS3 camera will be replaced by a CMUCAM5 camera)
- External 12V power supply (minimum 5A)

## Instructions:

Part | I: | Building | the | Air | Hockey | table

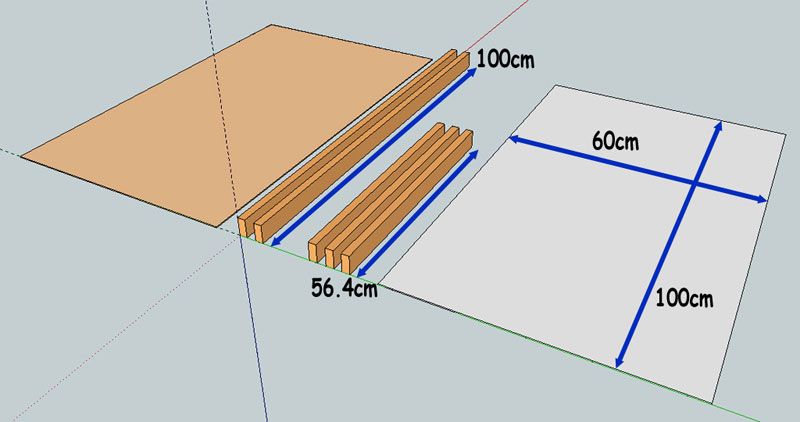
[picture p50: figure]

- Assemble the frame with wooden slats as shown in the picture. Use 3x30mm screws to attach the slats, one screw centered at the ends and two screws in the central reinforcement. It is always preferable to mark before with a pencil, then drill with a 1.5mm drillbit (to prevent the wood break) and then insert the screws. Use one of the 100x60cm boards to make sure you assemble it properly aligned. The screw heads must not protrude beyond the wood, we screw them until they are fully embedded in the wood.

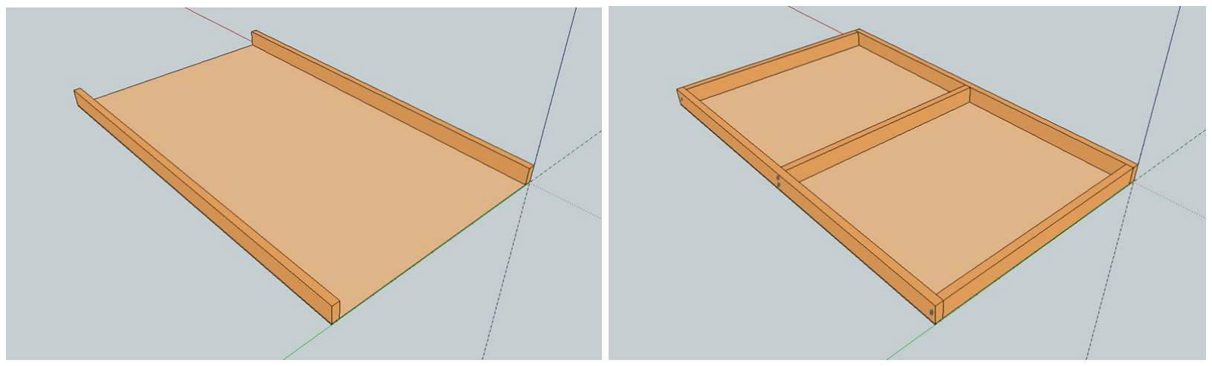
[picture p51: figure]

- Screw the 100x60cm board to the frame with some 2.5x16 screws (see photo). Start placing screws around the corner at 3cm from the edge and then approximately at 20cm distance (measure and make marks first, then drill with 1.5mm drillbit and then insert the screws)

- Now it´s time to open the air holes in the table. We are going to prepare a wood guide. The guide will be a 60x18x5mm wood slat with the holes. First let's mark the position of the holes. Leave a space of 3.75 cm at the edges and then mark every 2.5cm. In total we should have 22 marks. Now we make the holes with 1mm drillbit (Make sure the drill is well leveled)

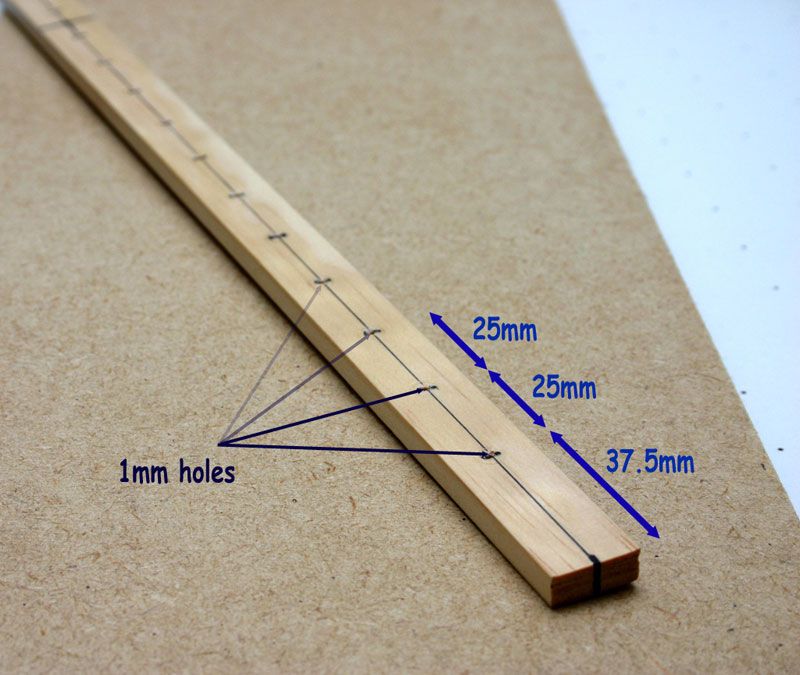
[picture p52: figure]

- Now it´s time to make the marks in the board flanges. Important, start from the center of the table (measure it) and make the first mark at 12.5mm on each side of table center. The idea is that in the center we will NOT make holes because we have the center wood slat. Now make marks on the board every

25mm until the edge where we leave a gap of about 6cm. We would have a total of 36 marks in the table (18 on each side of center)

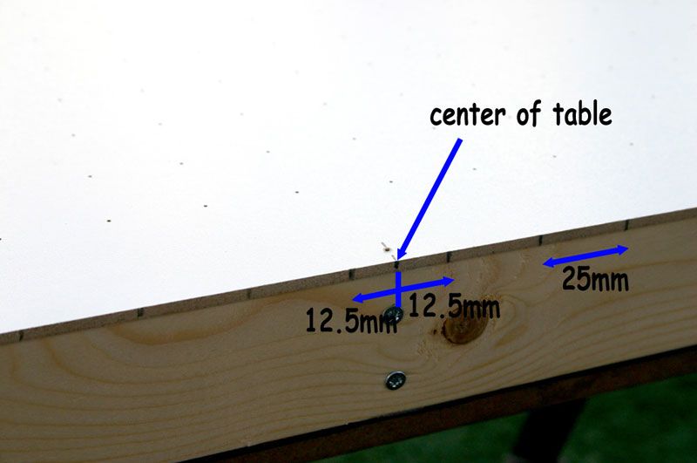
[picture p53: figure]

- Place the guide aligned with the marks, secure with tape on each side, press the guide against the table with your hand and started to drill the holes with the 1mm drillbit (22 in each row). We move the guide to the next mark, secure with the tape again and continue making holes ... Looks like a huge work but it´s not so hard (less than 40 minutes)
Tip: Prepare everything to be on a high and comfortable posture.

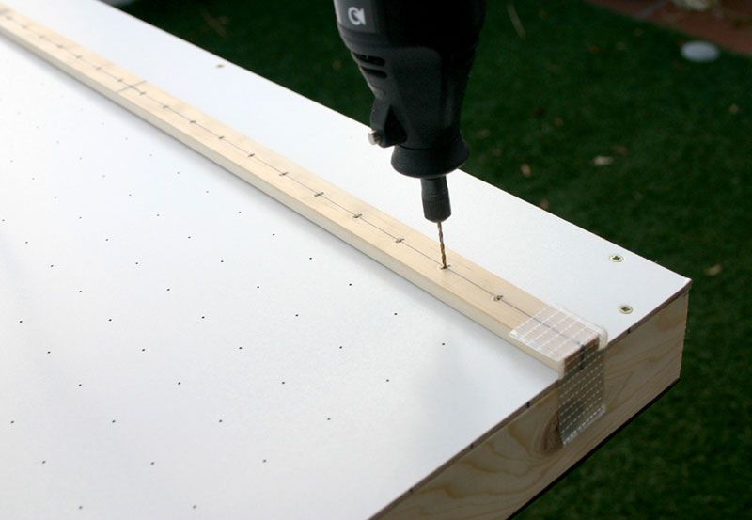
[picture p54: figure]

- Once finished the holes in the table, we will cover the slats on the backside of the table with EVA foam (typical craft material), including the center slat. We make this to seal the table (we want that the air could

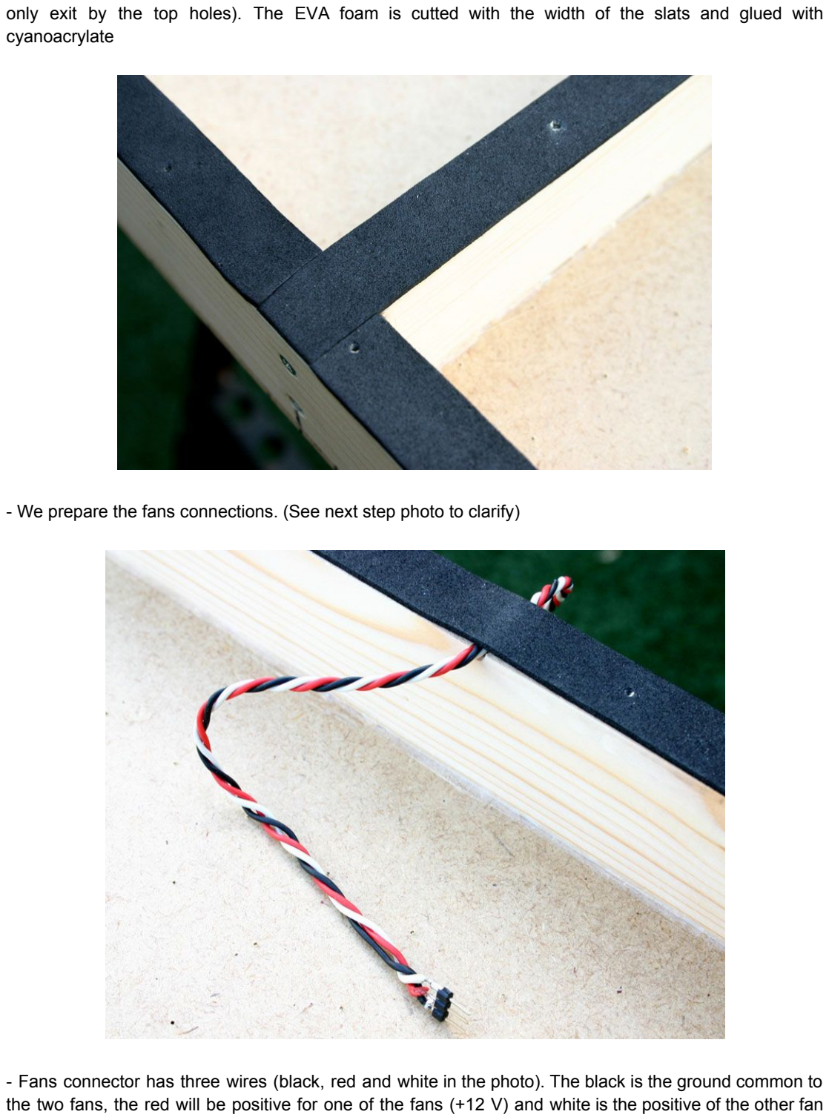
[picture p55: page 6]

only exit by the top holes). The EVA foam is cutted with the width of the slats and glued with cyanoacrylate

- We prepare the fans connections. (See next step photo to clarify)
- Fans connector has three wires (black, red and white in the photo). The black is the ground common to the two fans, the red will be positive for one of the fans (+12 V) and white is the positive of the other fan

(+12 V). Note: We only need +12V and gorund connections to the fans (red and black) but some fans have 3 or 4 wires. Sometimes +12V is the yellow cable. Try it first

- we seal the table on the backside with the hot glue gun so the air could not escape.

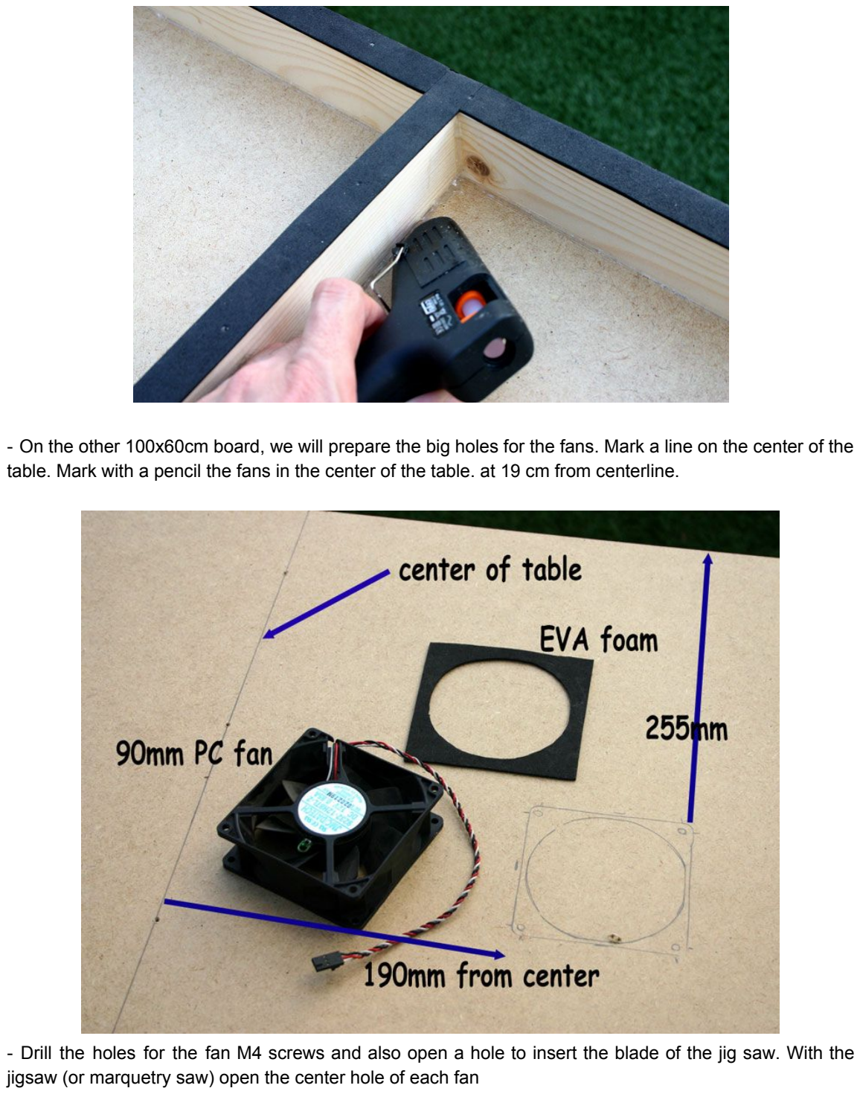
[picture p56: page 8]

- On the other 100x60cm board, we will prepare the big holes for the fans. Mark a line on the center of the table. Mark with a pencil the fans in the center of the table. at 19 cm from centerline.
- Drill the holes for the fan M4 screws and also open a hole to insert the blade of the jig saw. With the jigsaw (or marquetry saw) open the center hole of each fan

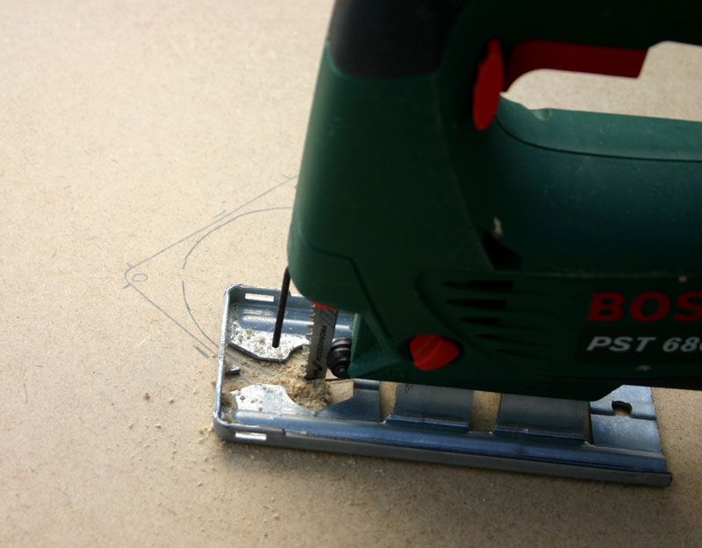
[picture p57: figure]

- Mark and cut the fan shape on the EVA foam with a 2cm extra margin. This will serve to seal the fan assembly
- Screw the fans (M4x12 screws and bolts) ensuring that the EVA foam seal properly and does not touch the blades
- Close the back board (with the fans) with the 2.5x16mm screws (not overtight the EVA foam, just a good seal). Don´t insert screws exactly in the corners (3cm apart is ok)

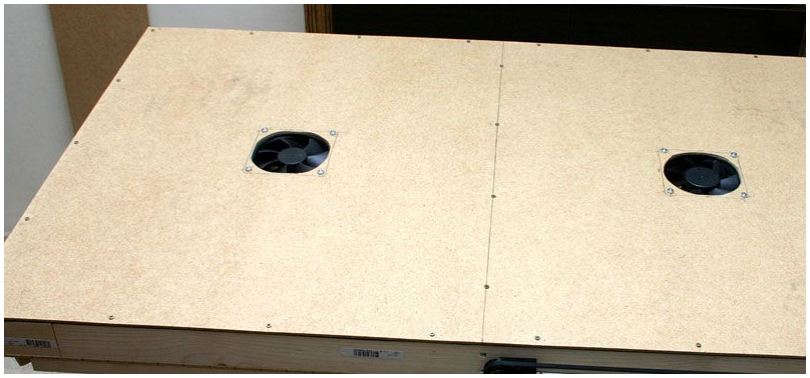
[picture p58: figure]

NOTE: Is recommended to add a grid to the fans to prevent childrens to hurt their fingers!.

- Now it's time to prepare the hockey sides To do this we take the 12x18 slats and cut the following

measures:
2 90cm for sides
4 12cm for rear parts, alongside the goals
4 6cm for corners
- Now we will cover the slats with 2 layers of EVA foam (glued with cianocrilate). We can use the wood slat to cut the EVA foam with a cutter (on the 18mm side). We need to layers for a good puck bounce. If you want you could round the sides near the goal.

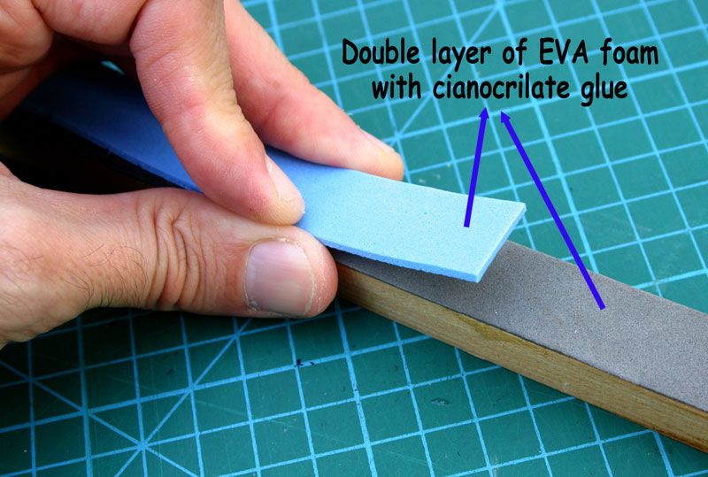
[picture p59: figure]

- Now we can screw it into the top of the table. As always first measure, mark, drill a hole and then insert the 3x30 screws. We will begin with the two long sides (90cm), then the back pieces and the corners.

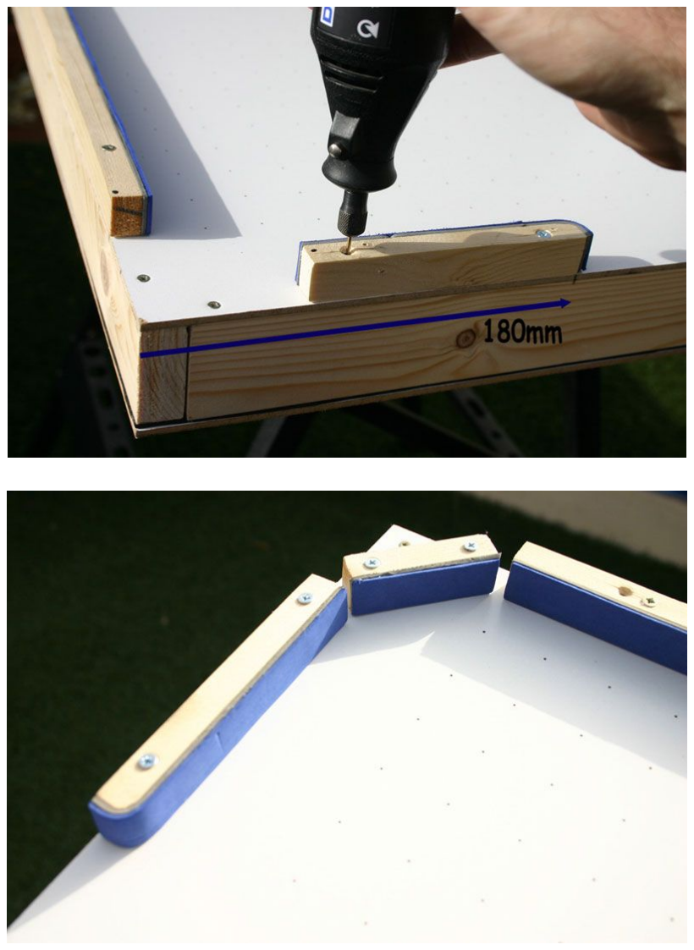
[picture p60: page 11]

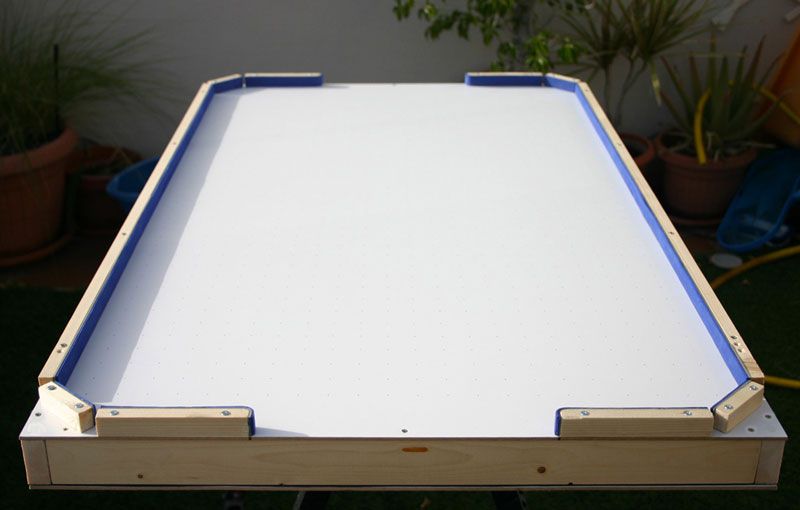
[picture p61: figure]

Well, we have an Air Hockey table ready! Connect a 12V input source 12V (check polarity - +) to the fans.

- Now it´s time to 3D print the pusher and the puck (files in repository).
The puck must be printed with the option of support material because it is hollow inside (cavity for the air in the bottom). Remove the support material and glue a circle of EVA foam in top side (I use green color). It´s recommended to put an adhesive felt on the bottom of the pusher to avoid scratching the table.

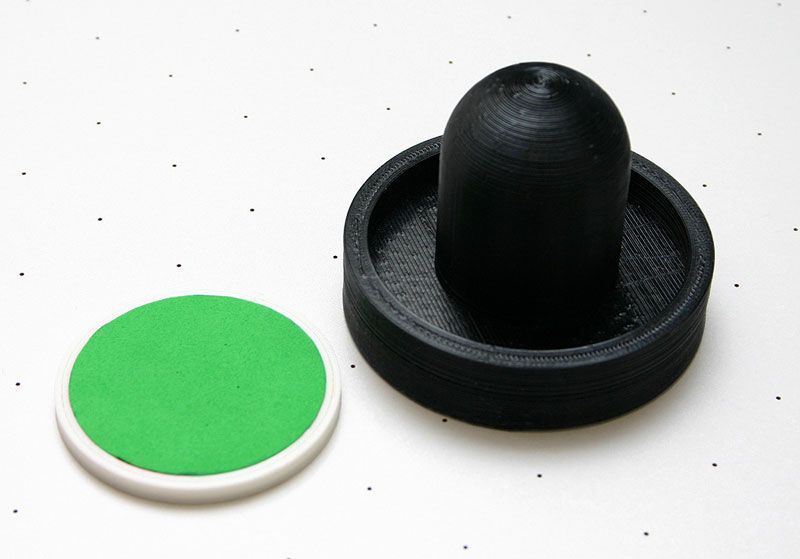
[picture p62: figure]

Turn on the fans (12V power), and it´s time to play and have some fun!!

Now we will begin construction of the Air Hockey Robot ...

PART | II: | Construction | of | Air | Hockey | Robot

Axes and motors definitios

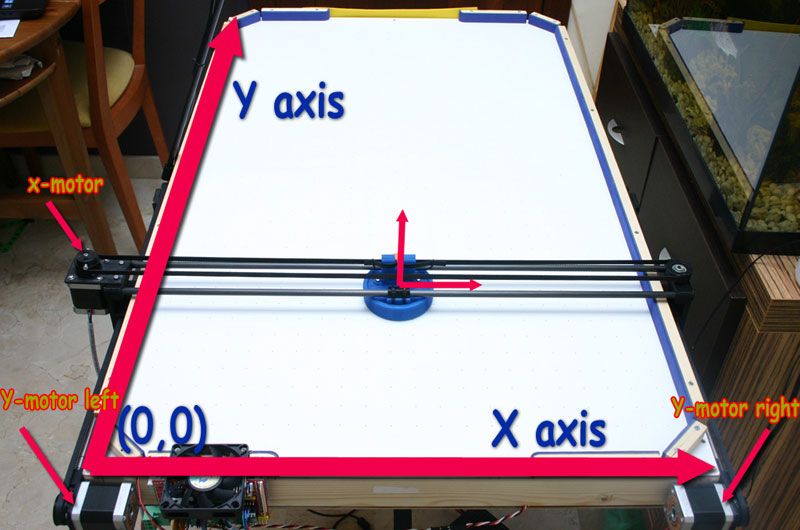
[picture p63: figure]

- Install the RAMPS 1.4 shield into the Arduino Mega
- IMPORTANT: We will modify the RAMPS for use ⅛ Microstepping on drivers. We must remove the JUMPERs shown in the photo. There are boards that do not have jumpers and we need to cut the traces with a cutter (carefully) between these two points. We could check the work with a tester. We repeat this for the drivers of X, Y and Z.

- Insert the stepper drivers with their coolers on the outputs X, Y and Z. The X output will go to the X axis, the Y output will go to the Y axis (left engine, seen from behind the hockey) and the Z output to the right motor.
- Motors. We make a flat part on the output shaft of the motor. The best method to do this is to place the motor on a bench table and use a file.

- Motor cables and conectors. The X motor should have a cable length of around 80cm, left Y-Axis should have a length of 30 cm and the right Y-axis must have a length of 58 cm. To extend the motor cables, solder a new cable with the appropriate connectors. You could buy cables with connectors (typical 3D printer cable set).
- Prepare the 12V power connector on RAMPS. The power supply sholud have 12-15V and a minimun of 5A power. OBSERVE POLARITY: Negative Black, RED positive!. We could also use a 12V battery or a li-poly battery 3S or 4S.
- Connect the Arduino USB cable to the computer. (Should install the appropriate driver if not already). Download the Arduino IDE (recommended 1.0.5 version). Select the Tools-> Arduino Mega 2560 board and tools-> serial port, serial port assigned to the arduino (example COM19).
Upload the sketch: AHR_Motor_Test.ino that is in the Utils / AHR_Motor_Test AHR project folder. (Downloaded from. ZIP project on github). Load into the arduino (Load button). It it´s load succesfully some lights should blink on start.
- Disconnect the USB cable from the Arduino and connect the 3 motor. (blue wire from the motors to the left side). Connect the 12V (RAMPS connector) and check for a few seconds, the motors start to rotate slowly. The X engine should turn in the direction of clockwise, the motor Y (Y-left) should rotate counterclockwise and Z motor (Y-law) should rotate clockwise. If any of the engine does not turn in the right direction we need to modify the code and comment / uncomment lines to reverse the directions of the motors:
# define INVERT_X_AXIS 1 / / axis Example X

unplug the power reload the program and test again. Later we will perform more tests...
Note: configuration updates that are made in the test application must be transfer to the final code that will be loaded into the robot.
- Setting the motors drivers power. Every motor driver has a small knob to adjust the power (motor current). At this point, if you touch the shaft of each motor with your hand, you should note that it´s quite hard and you are not able to stop it with your fingers easily. If not you should increase the power turning the knob on the driver clockwise slightly.

IMPORTANT: All this part of RAMPS, Arduino Mega + Engines + Drivers + + + drivers setting 12V is the same as 3D printers. If you have problems there are many tutorials and information on this subjects on the net

- Print the robot parts from repository. I've printed all in PLA plastic (I think it could work in ABS too). To print the GT2 pulleys you must have your printer very well calibrated (and print slowly). If you can not print the GT2 pulleys with enought resolution you have two options: Buy GT2 40 tooth pulleys or change to T5 belts because T5 pulleys are easier to print. In the repository there are al directory for T5 belt parts.
- Usually you need to finish the parts (specially screw and tube holes). Use a round file or even a threaded rod works well as a file. Be sure you have a good fit.

Y axis
We begin with the Y axis. The Y-axis has two sides, the right and the left. Both are fully symmetrical, and use the same parts. We start with the left side mounting the Y axis motor support.

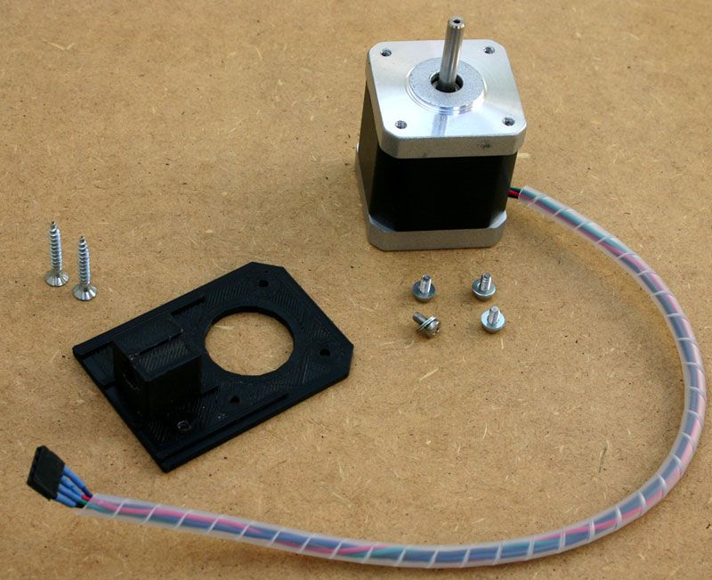
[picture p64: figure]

- Now we can screw the motor with M3x6 screws and using one or two washers. Now we can put the 42 teeth GT2 pulley on the motor shaft. The pulley must be mounted with the 2 M3 nuts inserted into their corresponding holes and M3x12 screws. One of the screws should match the flat part of motor shaft to ensure that the pulley does not slip on the shaft.

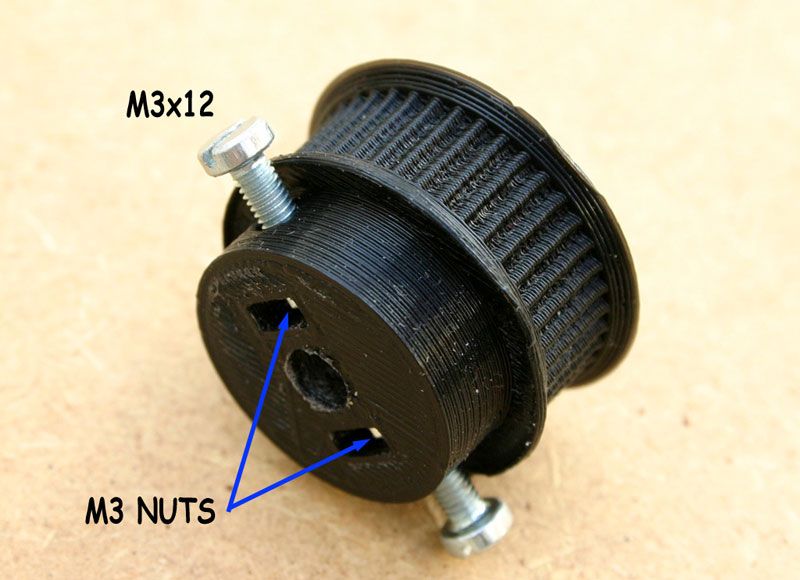
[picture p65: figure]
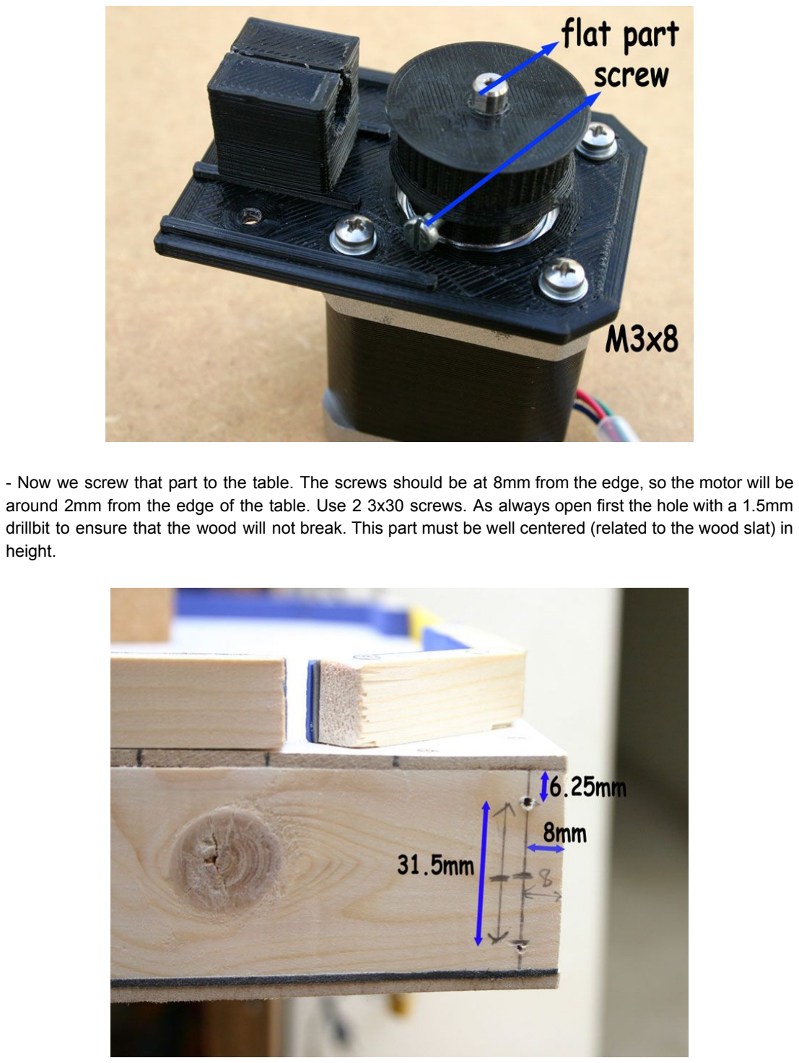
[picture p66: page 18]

- Now we screw that part to the table. The screws should be at 8mm from the edge, so the motor will be around 2mm from the edge of the table. Use 2 3x30 screws. As always open first the hole with a 1.5mm drillbit to ensure that the wood will not break. This part must be well centered (related to the wood slat) in height.

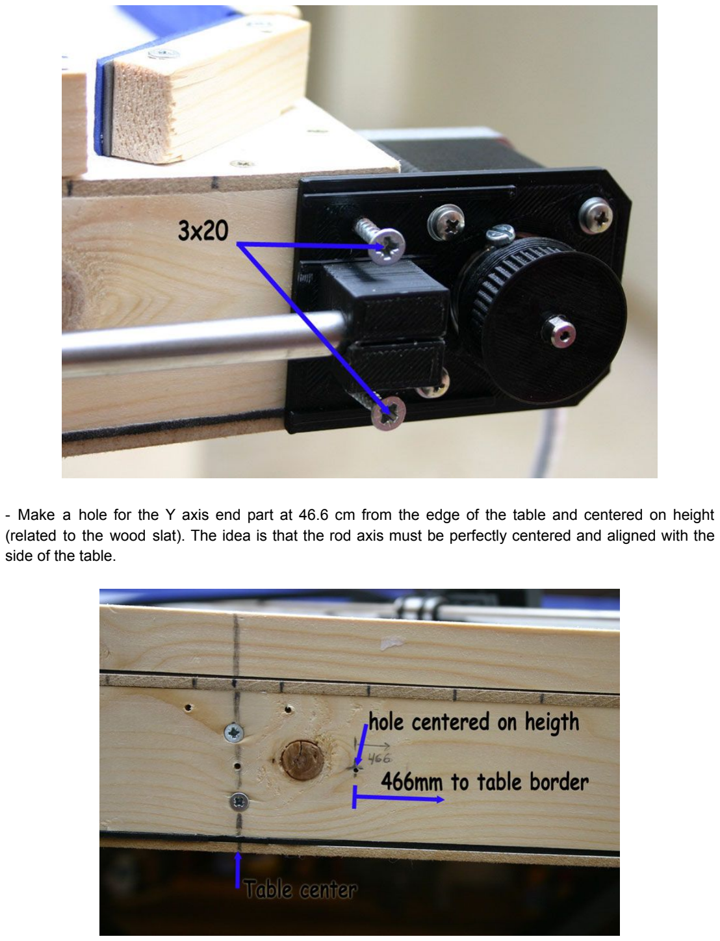
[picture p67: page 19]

- Make a hole for the Y axis end part at 46.6 cm from the edge of the table and centered on height (related to the wood slat). The idea is that the rod axis must be perfectly centered and aligned with the side of the table.

- Prepare the Y-carriage part inserting an LM8UU ball bearing and fasten with 2 nylon tag fasteners (the piece is ready for mounting one or two bearings but one is enough). I have mounted one bearing on the Y-left side and two bearings on the Y-right side.

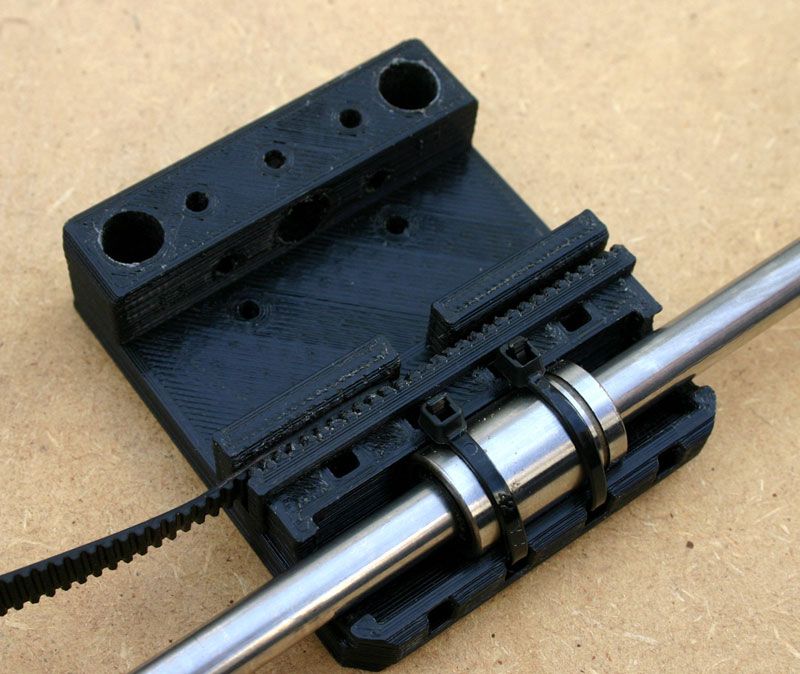
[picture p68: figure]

- Insert the Y-carriage into one of the 46cm steel rods. Insert the rod into the motor-mount part and then into the Y-axis end part. Screw the Y-axis end part with one 3x30 screw into the table. Check that the Y-carriage moves properly with little friction along the rail.
- Now it´s time to mount the other pulley (smooth) at the end part. the pulley is mounted in a 608 bearing with a small 24mm aluminum tube. If there are some clearance between the bearing and the pulley we can glue it together. Now install the pulley on the end part (the belt will prevent it to fall). Now mount the GT2 belt around the two pulleys and fasten to the y-carriage using the belt slots. The belt should be tight enough. Verified that the carriage moves and drag the belt correctly and the motor turns ok but the belt does not slip on the motor pulley. If the belt slips, you need to tighten the belt or maybe your pulley is not printed correctly and the belt slide. Maybe you need to print a higher quality piece or upgrade to T5 belt and pulleys that are easier to print (or buy some metal GT2 40 tooth pulleys).

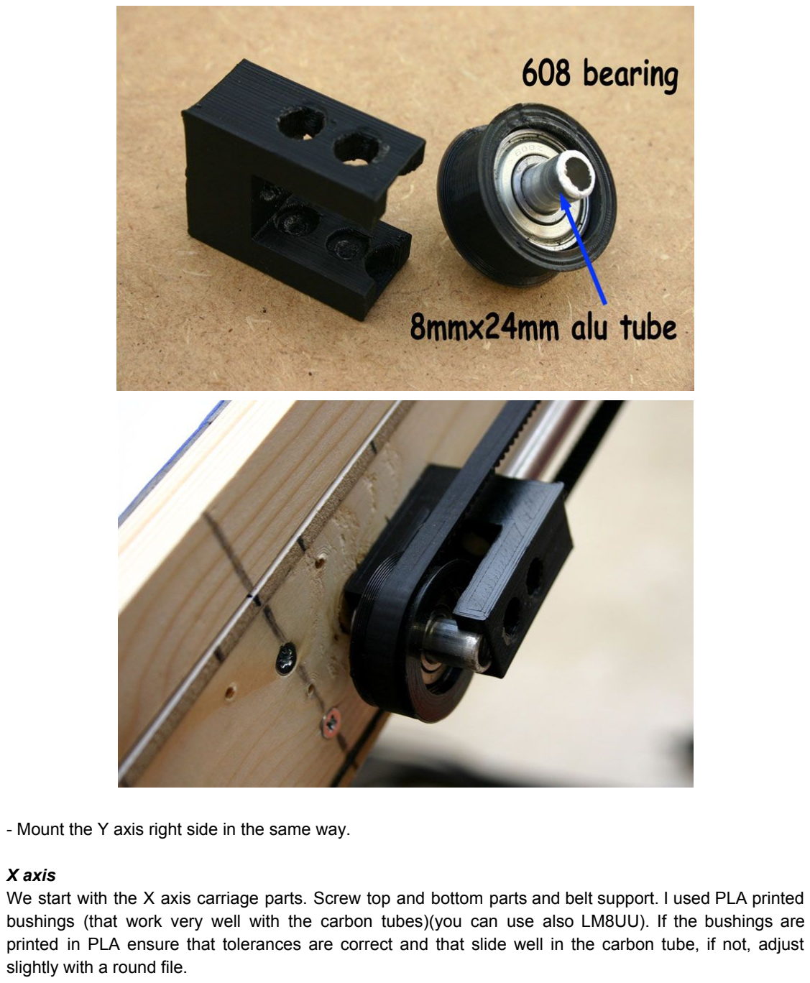
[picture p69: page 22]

- Mount the Y axis right side in the same way.

X axis
We start with the X axis carriage parts. Screw top and bottom parts and belt support. I used PLA printed bushings (that work very well with the carbon tubes)(you can use also LM8UU). If the bushings are printed in PLA ensure that tolerances are correct and that slide well in the carbon tube, if not, adjust slightly with a round file.

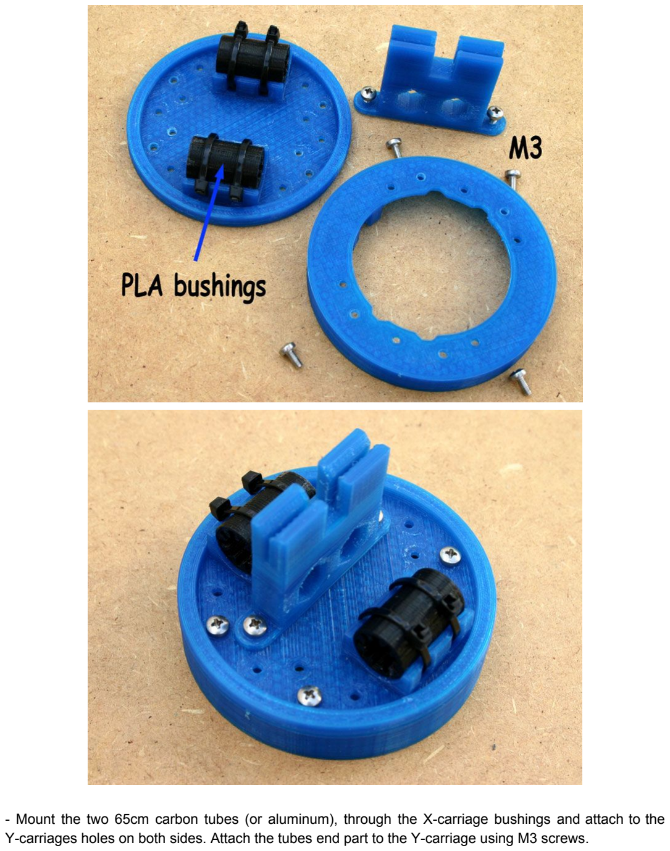
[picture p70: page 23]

- Mount the two 65cm carbon tubes (or aluminum), through the X-carriage bushings and attach to the Y-carriages holes on both sides. Attach the tubes end part to the Y-carriage using M3 screws.

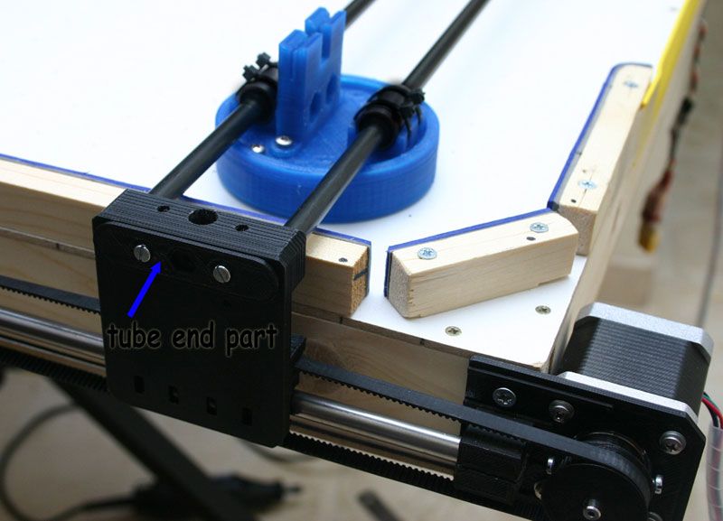
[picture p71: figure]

- Check that the X carriage moves freely in the tubes with low friction and very important: the carriage should hace a clearence with the table of around 2mm all the time. It is very important that the carriage don´t touch the table at any point.
Optionally (recommended) you can glue some EVA foam strips to the front of the car X (which will hit the puck) for a better rebound.
- Mount the X axis motor support and screw it to the Y-left carriage with two M3x20 screws with nuts Place the X motor with M3x6 screws and washers.

- Insert the 42 tooth GT2 pulley on the motor shaft, as we did with the other motors. At the other end mount the toothless pulley with a 608 bearing and the 30mm aluminum tube inserted into the Y-carriage.
- Mount the X axis belt, hold the belt on the X carriage belt slot and check that is tight enought Try to move the carriage and check that the belt doesn´t slip on the motor pulley.

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
tly in

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
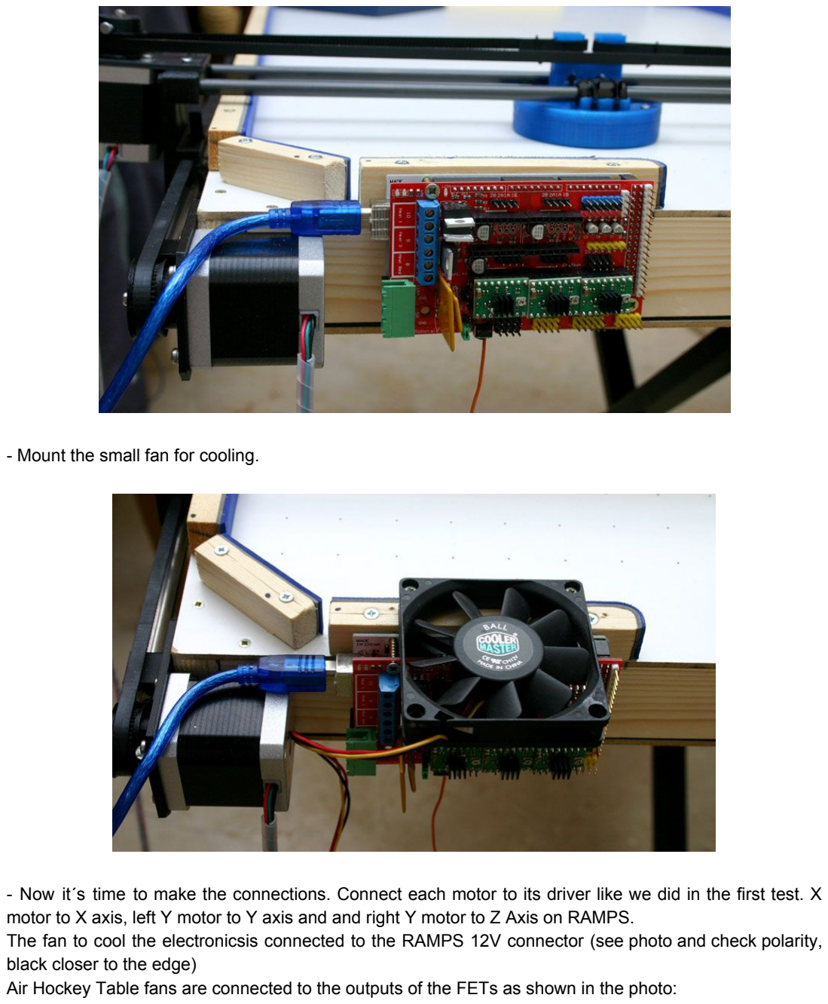
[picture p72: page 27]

- Mount the small fan for cooling.
- Now it´s time to make the connections. Connect each motor to its driver like we did in the first test. X motor to X axis, left Y motor to Y axis and and right Y motor to Z Axis on RAMPS.
The fan to cool the electronicsis connected to the RAMPS 12V connector (see photo and check polarity, black closer to the edge)
Air Hockey Table fans are connected to the outputs of the FETs as shown in the photo:

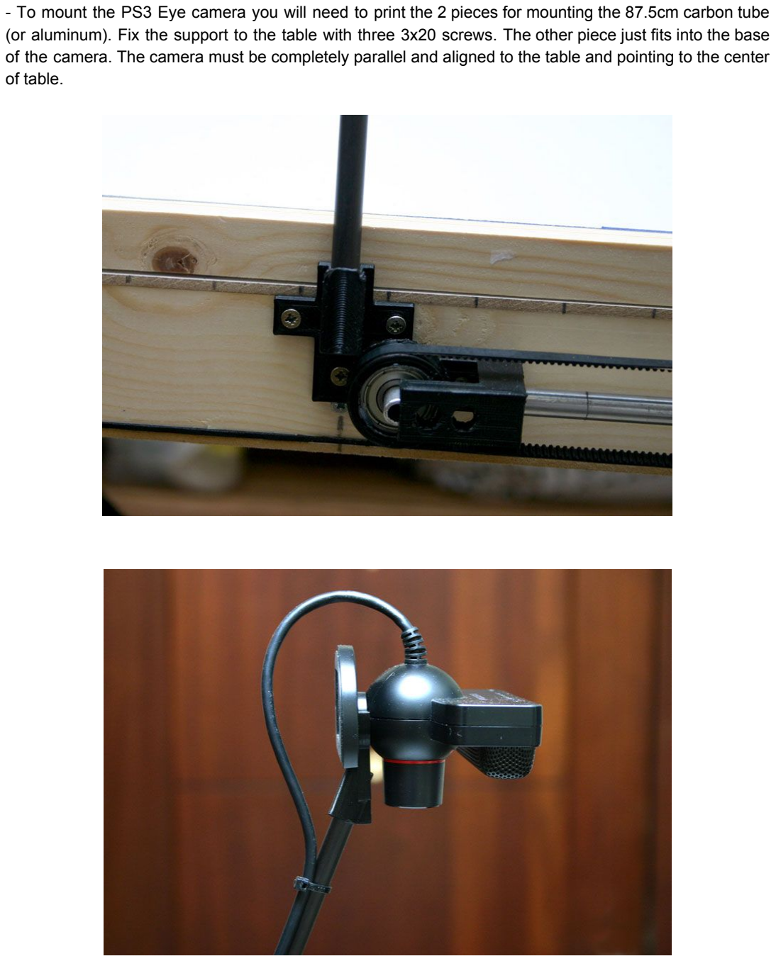
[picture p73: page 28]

- To mount the PS3 Eye camera you will need to print the 2 pieces for mounting the 87.5cm carbon tube (or aluminum). Fix the support to the table with three 3x20 screws. The other piece just fits into the base of the camera. The camera must be completely parallel and aligned to the table and pointing to the center of table.

### Tests:

- Motor test.
Load the code AHR_Motor_Test.ino (Utils / AHR_Motor_Test folder) into the Arduino.
Before connecting the power supply (12V) to the robot, move the robot manually (by hand) at about the middle of the work area.
Connect the power supply and the robot should begin (after a few seconds) a smooth movement in the X axis toward the positive direction of X axis (to the right). The robot should move exactly 5cm.
If the robot moves in the opposite direction, disconnect power, modify the line in the arduino Configuration.h file:
/ / # define INVERT_X_AXIS 1
and we take the comments to invert the X axis:
# define INVERT_X_AXIS 1

Check if the robot has moved 5cm (if the pulleys and belts used are the project should be so) Otherwise you would have to modify the line:..
# define X_AXIS_STEPS_PER_UNIT 19

If you use 40 tooth GT2 pulleys or 16-tooth T5 pulleys the “19” should be replaced by “20”.
If the robot moved approximately half way (2.5cm) check the microstepping of the drivers.

Within seconds the robot starts a movement in the direction of the positive Y axis (forward) Again if the robot moves in the opposit direction (Y axis has 2 motors) change the appropiate line: If the motor that does not move correctly is the Y-left motor then:
# define INVERT_Y_AXIS 1

If it´s the Y-right motor:
# define INVERT_Z_AXIS 1

Check that the robot moves exactly 5cm again. If not change this:
# define Y_AXIS_STEPS_PER_UNIT 19

Remember that any change in the Configuration.h file made in this test must be copied to the final code loaded into the arduino (AHRobot Configurations.h file)

In this test the motors will move very slowly, if still any of the motors lose steps (not able to move and makes a strange noise) you will have to increase the power on the driver of the motor (slightly turning the potentiometer driver in clockwise direction)

- Motor | speed | and | acceleration | test.
Load the code named AHR_Motor_Test_X.ino this in Utils / AHR_Motor_Test_X folder
Again move the robot to the middle of the workspace.
Turn the power on and the robot within a few seconds shouldl move in the X axis, first slow and then fast. Check if the robot loose steps (noise and loss of position). To correct start increasing (very slowly) the power of the X motor driver (not too much or it will overheat)
If the robot still loose steps decrease the acceleration on this axis :
# define MAX_ACCEL_X 280

decrease by 20 units and try again...

Check also (by removing the motor belt) that the robot is able to move freely and with very little friction along the entire axis and it never toch the table.

Now the same with the Y axis:
Load AHR_Motor_Test_Y.ino code (Utils / AHR_Motor_Test_Y folder)
With power off move the robot manually to the center on X axis and the minimun position (it reaches the stops) on Y axis (totally backward). Power on.
Same as before, if the robot loses steps in one of the two engines of the axis, Power off, increase poweron drivers or decrease acceleration:
# define MAX_ACCEL_Y 140

also check that all the robot can move without friction on this axis.
- Camera | install | and | color | calibration
First install PS3 camera drivers from:
http://.codelaboratories.com / products / eye / driver /
We will make the camera tests with the arduino disconnected.
The zoom of the PS3 camera should be in the blue dot position (wide angle)
The vision system must clearly recognize two different colors, one for the puck (eg green) and one for the robot (for example orange). Use preferably very saturated colors because they that are easy to recognize. We use EVA foam because it´s matte, avoid bright colors.
Load the application (on PC) CHECK_HSV.exe. A screen will appear with some controls to define the ranges of H (color), S (saturation) and V (value) We will properly adjust the values to correctly detect the puck. Then we will adjust to detect the robot color.
Reference values for green EVA foam:
Reference values for orange EVA foam:
The vision system needs light! so be sure you have enough light power on the robot area.
We check that the color is recognized correctly, and we don´t have too much external "noise". We check aso that some slightly variations on lighting conditions, for example, if we put the puck under the shadow of the camera itself, it could recognize the color. If not, play with the controls to get the appropriate values Get the parameters for puck and robot.
- | Final | check | of | the | camera
with the previously captured values we will modify the file AHR.bat editing it:
COM19 AHR.exe 70 94 60 150 10 146 5 20 110 200 90 200 60
The first value "COM 19" is the serial port where the Arduino (the same we use to load the code on arduino IDE) The following first 6 values correspond to the range to detect the disk and the other 6 to ranges to detect the robot (which we have selected in the previous step) The last value "60" are the Frames per second of the vision system.
Run AHR.bat and should appear something like the photo
The camera must be aligned and pointing to the center.
The robot should appear on the right side of the picture.
Place the puck in the exact center of the table, we should see that the robot marks the correct position: 300mm in X and 500mm y Y:
Otherwise, move the camera to get something like what is shown in the picture

We should move the puck and the coordinates must be correct (about 1cm error). If not check that the camera is well aligned, the camera tube has the right dimension and if not you could start to play with this parameter in the Configuration.h (read the code comments):
#define CAM_PIX_TO_MM 1.4

And… | Let´s | play!!
Load the final arduino code: AHRobot.ino ( AHRobot folder)
Remember that if we have changed any parameter in the Configuration.h file for robot calibration, verify that these changes are properly copied to the Configuration.h file in this project.
Before power on the robot, we always start the game moving the robot manually to the start position that is: minimun of Y axis and centered on X axis (can be marked in the table.) This will be always the starting position when we reset or boot the arduino!. The code needs to know that the robot is in this position at the beginning.

Power onthe robot (12V), wait a few seconds and the robot will move to the defense position.
On the PC Start the AHR.bat, wait until you see the image ... and start playing!

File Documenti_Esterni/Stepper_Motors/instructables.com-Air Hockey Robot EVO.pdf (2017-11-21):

# Air Hockey Robot EVO

### Introduction: Air Hockey Robot EVO

instructables.com /id/Air-Hockey-Robot-EVO/ (http://www.instructables.com/id/Air-Hockey-Robot-EVO/)

A challenging robot, perfect to have fun and learn robotics at the same time

It is fast, stable, easily modifiable and shares the electronics and ancillary elements with others jjRobots like the iBoardbot, (https://www.instructables.com/id/IBoardbot-the-Internet-Controlled-Whiteboard-Robot/) B-robot EVO. (https://www.instructables.com/id/B-robot-EVO-the-Self-Balancing-Robot/) Sphere-O-Bot (https://www.instructables.com/id/Sphere-o-bot-a-Friendly-Art-Robot/) (and more to come!)

With the idea of using standard 3D printer parts : NEMA17 stepper motors (http://www.jjrobots.com/product/stepper-motor-nema17/), stepper motor drivers (http://www.jjrobots.com/product/ardusplay-stepper-motor-driver-a4988/), the jjRobots Brain Shield, belts , bearings, rods, 3D printed pieces … we started to develop the project. The main advantage (https://jjrobots.com/product/b-robot-electronic-brain-shield-v2-0/) of using these parts is that they are inexpensive and easily available. We have chosen a medium size Air Hockey table from a well known online seller (https://www.athleteshop.com/buffalo-mini-airhockey-table-explorer) to deploy the robot on: We wanted something easily transportable but comfortable to play with. The final dimensions of this Air Hockey table are 90x43cm.

Step 1: The Air Hockey Robot EVO Has Been Seen At...

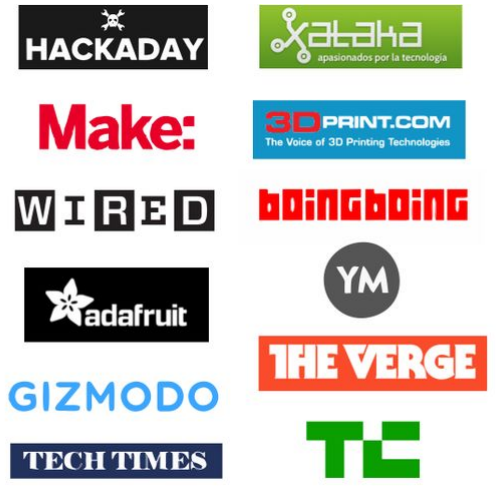
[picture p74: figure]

### Step 2:

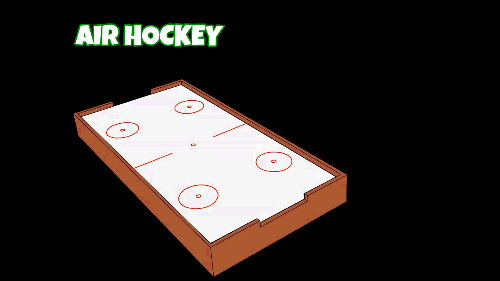
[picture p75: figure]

The Air Hockey Robot (http://www.jjrobots.com/air-hockey-robot-evo/) consist in three different parts: The Air hockey table, the Robot itself and your own smartphone.

Your smartphone, running the Air Hockey Robot APP (free APP) (https://play.google.com/store/apps/details?id=com.jjrobots.ahr_evo_mobile&hl=en_GB) , can detect features on the playing court and make decisions according to the detected objects location and theirs trajectories (and attack/defend in consequence).

### Step 3: HOW DOES THIS ROBOT WORK?

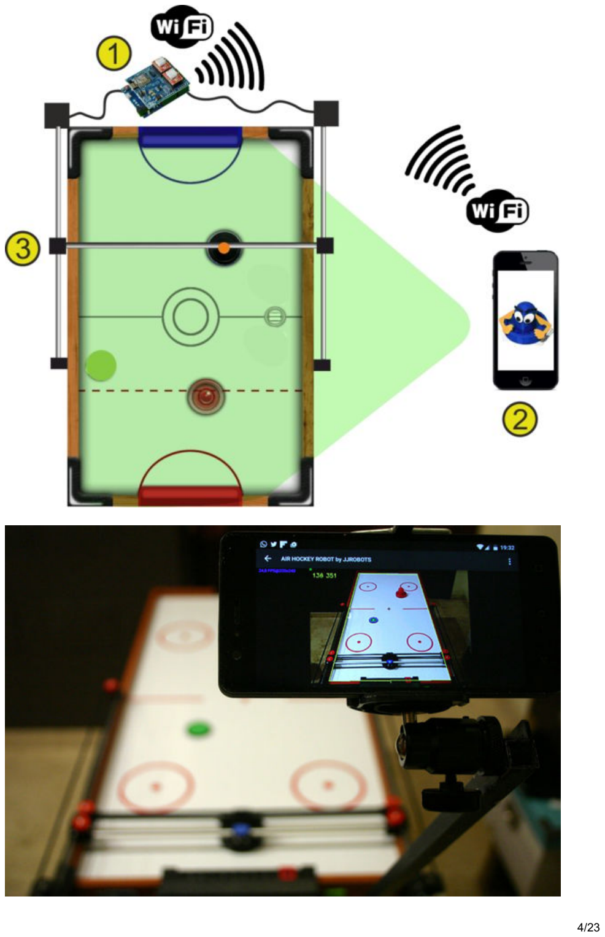
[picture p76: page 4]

The smartphone´s camera(2) is looking at the playing court . The camera´s captured data is processed in real time by the smartphone. Detecting the position of the puck and the “Pusher robot” (and according to the current location of all the elements on the court), your smartphone makes decisions and commands the Robot (3) via WIFI (1).

Your smartphone will become an augmented reality device, showing predicted trajectories and position of all the objects involved in this game. The Robot is locally controlled by the jjRobots Brain Shield (1) (http://www.jjrobots.com/product/b-robot-electronic-brain-shield-v2-0/) which dictates the speed and acceleration of the robot, sending the appropriate pulses to the stepper motors. Easy!

### Step 4: CONTROLLING THE ROBOT

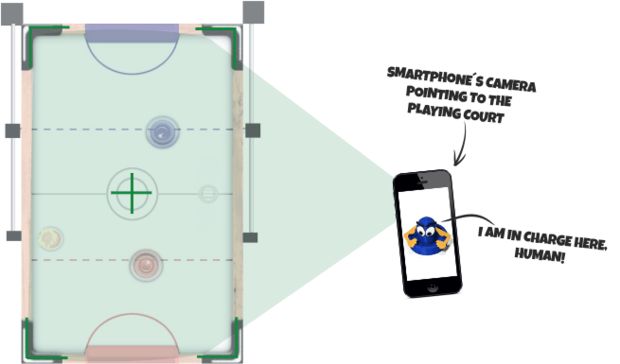
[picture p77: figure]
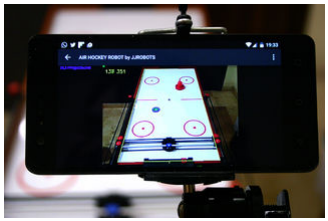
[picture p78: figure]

We have developed an APP to control the Air Hockey Robot. It is freely available on Google Play. (https://play.google.com/store/apps/details?id=com.jjrobots.ahr_evo_mobile#details-reviews) The idea was to use the portable computer that you have "always" with you (we are talking about your smartphone :-D ) to control the Robot. As the smartphone already has a good camera and extremely powerful processor, why not making the most of it?

There are two options to control the Air Hockey Robot: Let your smartphone control it ( AUTO) or the Manual control: take control of the robot using your finger (move the robot wherever you want). Feel free to download the APP and check both options (you do not need the hardware to play with the APP.) (https://play.google.com/store/apps/details?id=com.jjrobots.ahr_evo_mobile&hl=en_GB)

If you download the APP keep this in mind: As the smartphone (in order to control the game) will look for two different things (the robot and the PUCK locations) two different small circles (green and blue foam circles) will tell where both elements are in the playing court. Take a look to the photos showing the foam circles. The APP can be set to detect any other colour instead the default ones (via the setting menu) but the diameters have to be: 2 cm for the robot, and 4 for the PUCK. If you print the 3D parts by yourself, do not use the same colours used for the foam circles or the robot will get confused!

NOTE: The APP will celebrate if you score and have funny sounds of the crowd cheering up when the puck speed up :-D

### Step 5: How to Create One. STEP 1: What You Need. BOM

If you want to support jjRobots, you can get the OFFICIAL Air Hockey Robot EVO KIT from here (http://www.jjrobots.com/product/air-hockey-robot/) . Optionally you can get everything by yourself and manufacture the jjRobots Brain Shield (http://www.jjrobots.com/product/b-robot-electronic-brain-shield-v2-0/) (info available here). (https://github.com/jjrobots)

We have published an ASSEMBLY GUIDE here. (http://www.jjrobots.com/air-hockey-robot-evo-assembly-guide-v-1-2/) The FORUM (http://forums.jjrobots.com/forum-4.html) is always available too for everyone who wants to share ideas and ask for help.

A short FAQ about the robot here (http://www.jjrobots.com/air-hockey-robot-evo-frequently-asked-questions-faq/)

BILL OF MATERIALS:

### Step 6: Some Comments Before Proceeding

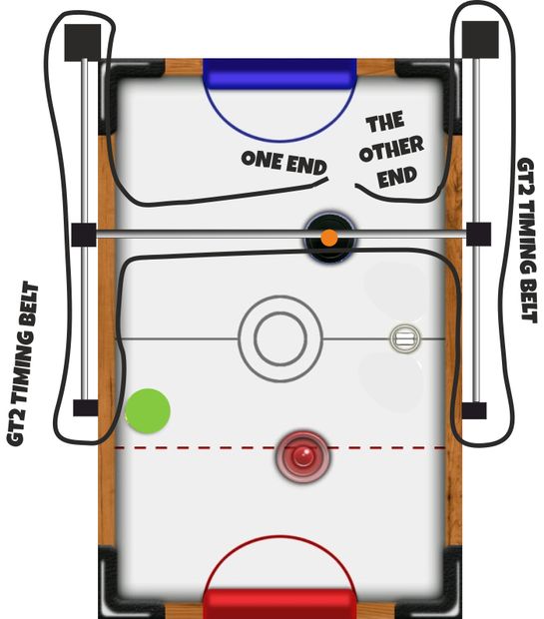
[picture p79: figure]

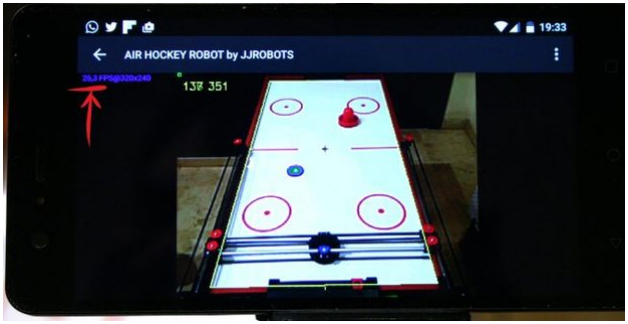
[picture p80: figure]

The key for assembling a flawless working robot is the H-bot system: this structure allows the robot to move itself to any location on its playing field only using two motors. Can be detached easily so you can use the Air Hockey robot as a Air hockey table whenever you want.

You need this H-bot to run smooth and be strong at the same time. The better you set it up, the higher the accelerations you can reach with your robot. Pay attention to the tips provided throughout this guide. The other thing to be aware of: vision system. The smartphone camera is capable of capturing up to 30 frames per second. Doing that, the robot can calculate precisely the position (and in consequence, its trajectory ) of both the robot and the puck.

VISION SYSTEM: The coordinates of the puck and its trajectory are calculated using the visual data coming from the smartphone´s camera . Two consecutive frames are required in order to calculate the trajectory of the puck. The Air hockey robot uses its current location, the puck position and the trajectory prediction to determine its strategy – either defence, defence and attack, or a new attack. An uniform illumination is extremely important for the vision system. Avoid shadows, reflections (and if you can, fluorescent lighting).

The Air Hockey robot uses two powerful stepper motors. Keep an eye on where you place your fingers!. Sudden accelerations of the robot within its playing area could catch you unaware. Before adjusting anything remember to disconnect its power supply.

Remember to print the parts listed in the Thingiverse (https://www.thingiverse.com/thing:1804534) webpage (or get them from us) (http://www.jjrobots.com/product/air-hockey-robot/) before the set-up process

Assembling the robot might take from 40 min to nearly 2 hours. The most important thing: the h-bot structure has to move smoothly. If you notice friction, use olive oil.

### Step 7: Assembling the H-bot Structure

Assuming you have already printed all the parts and have all the hardware. Lets start with the H-bot structure.

Use 6x 6mm M3 bolts (3 per motor) to fix the motor to the motor supports

Place the 623 ball bearings (12 units, 2 per pulley) inside the plastic pulleys as indicated above.

### Step 8: Fan: Cooling Down the Electronics

Use 4x 15mm M3 bolts and 4 M3 nuts to fix the FAN to its support

### Step 9: Horizontal Axis

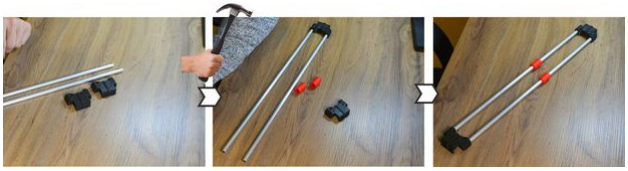
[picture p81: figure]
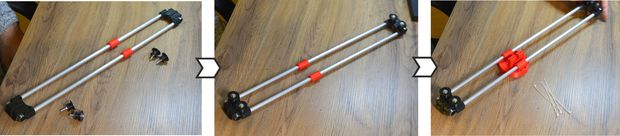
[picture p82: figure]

Take the 2 aluminium pipes and insert both in the LATERAL SLIDER piece. This is the most important part of this assembly guide. It could seem quite hard to insert the pipes into the 3D printed parts, but the sturdiness of the structure will depend on how tight everything is. Use
a hammer (gently) if you want to push the aluminium
pipes into the channel. Twist the pipes as you are

pushing them could help during the insertion. Before placing the second LATERAL SLIDER cap, insert the bushings (red in the photo above)

Now it is time to screw the pulleys you have assembled before. There is no need to use a nut to fix the bolts. Just screw them. Use zip ties to hold the pusher in place (x4). Just hug the plastic bushings with the zip ties as you run them through the pusher piece (there are two channels for that)

Check there is not friction on this structure. Olive oil will greatly reduce the friction between the aluminium and PLA plastic: https://www.jjrobots.com/wp-content/uploads/2016/12/checking-movement.mp4

### Step 10: Robot Pusher

Use 4x 15mm bolts to fix the base of the PUSHER. All the photos above show how it looks after placing it

### Step 11:


Now, take 4x M3 10mm bolts + 4 nuts to fix the pulleys to the motors axis. They have to be tight. These pulleys will transmit all the movement to the robot. If they are loose, the robot will misbehave.

side supports. Use a pulley (the ones with the 2x 623 ball bearings inside) and fix it the both side supports using a self-locking nut. Once finished, insert the steel bar into the side support.

### Step 12:


We are almost finished here. Insert the LM88UUs into the steel bars as indicated above. Do not forget this step!

After placing the linear bearings (LM88UU), insert the steel bars into the motor´s support. Now you are ready to set everything on the Air hockey table.

NOTE: the "default" Air hockey table used for this robot is one worldwide available, distributed by Athleteshop. (https://www.athleteshop.com/buffalo-mini-airhockey-table-explorer) But you do not really have to get this one. The Robot can be adjusted to any others air hockey tables with similar dimension (90x40 cms) there is not limitation on the APP side. The limitation comes with the hardware: the motors and H-bot structure will not be able to handle a 2x1 meter air hockey table.

### Step 13:


Screw off the top screw and place the motor support in place. There is video here: http://www.jjrobots.com/air-hockey-robot-evo-assem... showing up how to do this step (We can not upload it to the Instructables webpage) (http://www.jjrobots.com/air-hockey-robot-evo-assembly-guide-v-1-2/)

Fix the side supports using two wood screws.

### Step 14:


Push, gently, the X-axis robot structure into the LM8UU linear bearings. Check the video here (http://www.jjrobots.com/air-hockey-robot-evo-assembly-guide-v-1-2/)

### Step 15: HARDWARE/ ELECTRONICS

Electronics: Elements needed to control the Robot: jjRobots Brain Shield (http://www.jjrobots.com/product/b-robot-electronic-brain-shield-v2-0/), Arduino Leonardo (http://www.jjrobots.com/product/arduino-leonardo-clone-usb-cable/), 2x Stepper motor drivers (+heatsinks), FAN (12v) and 3D parts support + bolts/nuts (http://www.jjrobots.com/product/ardusplay-stepper-motor-driver-a4988/)

In the photo: All the electronics correctly set. Pay attention to the stepper motor drivers orientation.

### Step 16:


Use 3 screws to fix the Arduino Leonardo to the Air hockey table (next to the motor). Then, connect the Brain Shield and finally, the stepper motor drivers.

Place the FAN on top of everything and connect it to the VIN output of the jjRobots BRAIN SHIELD. There is only one way to connect it, but just in case, take a look to the electrical diagram. Finally, connect the motor cables.

DOUBLE CHECK THE POLARITIES! The stepper motors can handle an inverted polarity but the FAN can not say the same.

NOTE:

Always, always keep the FAN blowing while the Air Hockey Robot is working. The stepper motor drivers might get damaged is there is not a constant air flow cooling them down


### Step 17: AIR HOCKEY ROBOT VISION SYSTEM (A.K.A. Your Own Smartphone)


Use three screws (location indicated by the yellow arrow) to fix the POLE SUPPORT to the Air hockey table. Place it 2 cms away from the edge where the Air hockey table´s Goal will be placed.

if you set the GOAL in place, you should have something like the photo above (note: the motors are not connected in the photo)

### Step 18: Placing the Smartphone As the Camera


Use a 25mm long bolt and a wingnut to hold the smartphone support to the pole. Fix the smartphone holder using the camera bolt too. The camera of the smartphone has to be on the left side (pointed by the red arrow on the photo above)

Install the control APP (https://play.google.com/store/apps/details?id=com.jjrobots.ahr_evo_mobile) and start it up. Place the smartphone on the holder and point to the playing court. Take a look to the video in the assembly guide to know how to calibrate (http://www.jjrobots.com/air-hockey-robot-evo-assembly-guide-v-1-2/) the point of view

NOTE:
In order to connect the APP to the Air Hockey Robot, you will need to connect your smartphone to the “JJROBOTS_XX” WIFI NETWORK using the password: 87654321


### Step 19: Creating the Colour Features: Things to Be Detected by the Robot


Cut the GREEN EVA foam with the shape of the PUCK (use it to draw its shape on the foam and then cut it). Stick it to the PUCK using the double side tape (provided with the KIT)

Cut a 20mm diameter circle of BLUE FOAM and place it as above. Use the double side tape to stick it.

Why using FOAM and not a 3D printed feature or…a sticker?

Due to the FOAM anti-reflective capacity. Keep in mind that the ROBOT VISION SYSTEM can be tricked by FAKE reflections on a plastic surface. The ROBOT is not just detecting a colour but two features: SIZE AND COLOUR

NOTE:

An uniform illumination is extremely important for the vision system. Avoid shadows, reflections (and if you can, fluorescent lighting).

### Step 20: PROGRAMMING THE ARDUINO LEONARDO


STEPS:

1. Download the ARDUINO CODE from HERE (http://www.jjrobots.com/wp-content/uploads/2016/12/AHRobot_EVO.zip) (or go to jjRobots GITHUB REPOSITORY (https://github.com/jjrobots/Air_Hockey_Robot_EVO/tree/master/Arduino/AHRobot_EVO) and download it from there)
2. Connect the USB cable provided to the Arduino LEONARDO
3. Compile the CODE using the ARDUINO IDE (https://www.arduino.cc/en/Main/Software) (The CODE is compiling and has been tested under ARDUINO IDE 1.6.12) and upload it

You have to select the ARDUINO LEONARDO as the default board and its PORT in the “TOOLS” MENU

### Step 21: CHECKING THE ROBOT H-BOT AND MOTORS


Well, it is time to check the Robot movement skills. The jjRobots Brain Shield has a button placed between the motors connectors

Push it if you want the robot to make a MOVEMENT
TEST PATTERN . This will let you know if everything is
fine with the structure and motor control. This is the first time you will see how the robot moves by itself, so do not place anything on the air hockey table and be careful with your fingers!

BEFORE TURNING IT ON: PLACE THE TIMING BELT IN THE H-BOT STRUCTURE. IMPORTANT: DO NOT TIGHTEN THE BELT TOO MUCH, CONTRARY TO THE “LOGIC” A VERY STIFF BELT WILL NOT LET EVERYTHING TO MOVE SMOOTHLY

1. If your robot is not making the TEST pattern, read below and find your problem:
2. The robot is crashing against one side of the air hockey table: check the polarity of the motor cables.


I am hearing a cracking noise coming from the motor/s and the robot does not move at all or not enough to draw the pattern: the stepper motors can not move the robot due to lack of power. This can be caused by:There is too much friction in the H-bot structure: Check everything again. Is the timing belt too tight? Try to adjust the STEPPER MOTOR DRIVERS output current via its potentiometer

MUCH MORE INFO AND TROUBLESHOOTING (updated) HERE: http://www.jjrobots.com/air-hockey-robot-evo-assembly-guide-v-1-2/ (http://www.jjrobots.com/air-hockey-robot-evo-assembly-guide-v-1-2/)

QUESTIONS, COMMENTS, PROBLEMS?. GET TO THE AIR HOCKEY ROBOT FORUM HERE (http://forums.jjrobots.com/forum-4.html)

### Step 22: GET THE AIR HOCKEY ROBOT KIT

We really hope you liked this robot. We have been working hard to make it... perfect for a community like Instructables. The APP has been created keeping in mind that it had to be compatible with many air hockey tables and configurations. All the Arduino code and hardware is OPEN SOURCE. If you have any ideas or comments, please let us know!

If you want to get the Air hockey hardware +ancillary elements + electronics + even the 3D parts from us:

You can get your customised KIT from here (http://www.jjrobots.com/product/air-hockey-robot/) (jjrobots shop)

Air hockey table (recommended but not the only you can use) here (https://www.athleteshop.com/buffalo-mini-airhockey-table-explorer)

Assembly guide + troubleshooting here (http://www.jjrobots.com/air-hockey-robot-evo-assembly-guide-v-1-2/)

Community here (http://forums.jjrobots.com/forum-4.html)

GITHUB repository here (https://github.com/jjrobots/Air_Hockey_Robot_EVO)

3D parts models here (https://www.thingiverse.com/thing:1804534)

Follow us on twitter to know updates of this robot and new OPEN SOURCE robots releases! Follow @jjrobots (https://twitter.com/jjrobots)

### Step 23: Other OPEN SOURCE Robots Created Using the Same Electronics + Ancillary Elements

iBoardbot: (http://www.jjrobots.com/the-iboardbot/)


The iBoardbot (http://www.jjrobots.com/the-iboardbot/) is a robot connected to the internet capable of writing texts and drawing with great precision. Also, it can erase in a quick and effective way. Send to your iBoardbot your information from any part of the world. As it has a multi-user interface you can also play and challenge your kids, use it as a collaborative notice board or as a twitter wall in your shop window.

B-robot EVO: (http://www.jjrobots.com/product/b-robot-kit-plug-and-play-robot-version/)

The fastest self balancing robot (remotely controlled
using your own smartphone). Take a look to its skills!

Looking for robotic challenges? Visit the B-robot EVO academy (http://www.jjrobots.com/the-academy/)

Control APP freely available in Google Play (https://play.google.com/store/apps/details?id=jjrobots.jjrobots_002&hl=en_GB)

Sphere-O-bot: (https://www.instructables.com/id/Sphere-o-bot-a-Friendly-Art-Robot/)

The Sphere-O-bot is a friendly art robot that can draw on spherical or egg-shaped objects from the size of a ping

pong ball to a large duck egg (4-9 cm). KIT here (http://www.jjrobots.com/product/sphere-o-bot/)

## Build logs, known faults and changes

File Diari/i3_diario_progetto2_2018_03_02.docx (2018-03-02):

# Diario di lavoro

Luogo | Scuola
Data | 02.03.2018

Lavori svolti

Giairo Mauro, Joey Biancardi:

Abbiamo messo a posto il programma: le costanti nel file “configuration.h” e controllato a cosa erano dovuti i problemi della scorsa lezione.

Abbiamo testato simultaneamente il programma sia in modalità manuale che con la videocamera fino a raggiungere il massimo compromesso perché il robot riesca a giocare al meglio in automatico e in manuale.

Alessandro Spagnuolo, Alessia Sarak:

Abbiamo montato e perfezionato il timer, mettendolo su una “vero board” e testandolo.

Alessandro Spagnuolo, Alessia Sarak, Giairo Mauro:

Abbiamo montato i nuovi pezzi, e abbiamo ricalibrato i driver sulla scheda JJRobots perché funzioni con i motori e gli diano la giusta potenza.

Alessandro Spagnuolo, Alessia Sarak, Joey Biancardi, Giairo Mauro:

Abbiamo testato il progetto giocando sia in manuale che automatico e filmando il tutto.

Problemi riscontrati e soluzioni adottate

Il programma funziona con un problema sulla telecamera dell’applicazione, non prende bene i colori, ma il problema è dato dalla luce che punta sul campo.

Punto della situazione rispetto alla pianificazione

Siamo in tempo dato che i professori ce ne hanno dato in più.

Programma di massima per la prossima giornata di lavoro

Completare documentazione e presentazione.

Nome progetto: Form di inserimento Dati Espoprofessioni 1/1

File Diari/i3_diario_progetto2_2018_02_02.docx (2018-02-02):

# Diario di lavoro

Luogo | Scuola
Data | 02.02.2018

Lavori svolti

Alessia Sarak, Joey Biancardi:

Abbiamo sistemato i pezzi che sono stati ristampati e rifinito il tavolo.

Giairo Mauro:

Ho lavorato un po' alla correzione della documentazione, e poi sul collegamento di arduino con il computer per poter fare il punteggio sul computer mentre i miei compagni aggiustavano la parte hardware del progetto, dopodiché ho provato a collegare Arduino a un alimentatore ma abbiamo avuto diversi problemi.

Alessandro Spagnuolo:

Ho creato un sito web che contiene il timer e il punteggio della partita corrente contro il robot, dove una volta finito collegheremo arduino con la pagina web utilizzando dei bottoni.

Problemi riscontrati e soluzioni adottate

Giairo Mauro:

Ho avuto problemi on il collegamento al computer di Arduino e con l’alimentatore perché non si riusciva a fare bene contatto tra i due cavi per attivarlo.

Punto della situazione rispetto alla pianificazione

Siamo in tempo dato che i professori ce ne hanno dato in più.

Programma di massima per la prossima giornata di lavoro

Completare il progetto.

Nome progetto: Form di inserimento Dati Espoprofessioni 1/1

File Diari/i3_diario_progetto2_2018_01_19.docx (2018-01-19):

# Diario di lavoro

Luogo | Scuola
Data | 12.01.2018

Lavori svolti

Alessia Sarak:

Ho lavorato sulla presentazione e sulla documentazione, infine ho anche messo a posto l’algoritmo di timer

Giairo Mauro:

Ho lavorato sulla documentazione.

Alessandro Spagnuolo:

Ho lavorato sulla presentazione e ho cercato di perfezionare il robot, però, avendo arduino mega invece di arduino leonardo, non sono riuscito a provare il codice finale.

Joey Biancardi:

Ha lavorato sulla presentazione.

Problemi riscontrati e soluzioni adottate

Giairo Mauro e Alessandro Spagnuolo:

C’è il problema dell’arduino sbagliato, cioè arduino mega, dato che abbiamo bisogno di arduino leonardo per fare in modo che l’applicativo funzioni.

Punto della situazione rispetto alla pianificazione

Siamo in tempo

Programma di massima per la prossima giornata di lavoro

Presentare il progetto

Nome progetto: Form di inserimento Dati Espoprofessioni 1/1

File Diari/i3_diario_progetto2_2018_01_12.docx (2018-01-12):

# Diario di lavoro

Luogo | Scuola
Data | 12.01.2018

Lavori svolti

Alessia Sarak:

Ho lavorato sulla presentazione e ho perfezionato l’algoritmo del timer, in seguito c’è stato un problema con il riconoscimento dei pezzi dell’Air Ice Hockey che abbiamo risolto colorandoli in modo differenti.

Giairo Mauro:

Ho lavorato sulla documentazione.

Alessandro Spagnuolo e Giairo Mauro:

Abbiamo lavorato sui motori, Barchi ci ha dato un programma da provare per testare i motori e poi abbiamo provato la calibrazione del tavolo.

Joey Biancardi:

Ha lavorato e perfezionato il tavolo.

Problemi riscontrati e soluzioni adottate

Giairo Mauro e Alessandro Spagnuolo:

C’è ancora un problema con il collegamento tra il telefono, quindi l’applicazione JJRobots e la scheda JJRobots collegata ad arduino mega, perché non riesce a prendere il Mac address del telefono.

Ci son stati problemi con l’applicazione che non vedeva il Puck e il Pusher ma attaccandoci dei pezzi di carta colorati abbiamo risolto.

Punto della situazione rispetto alla pianificazione

Siamo in ritardo di 1 settimana

Programma di massima per la prossima giornata di lavoro

Finire la presentazione e i motori

Nome progetto: Form di inserimento Dati Espoprofessioni 1/1

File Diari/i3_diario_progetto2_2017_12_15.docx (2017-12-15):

# Diario di lavoro

Luogo | Scuola
Data | 15.12.2017

Lavori svolti

Alessia Sarak:

Ho lavorato sull’algoritmo di punteggio.

L’idea iniziale è quella di mettere due bottoni, uno a destra e l’altro a sinistra, con su scritto quale bottone appartiene a quale giocatore. Ogni bottone deve incrementare di uno il punteggio del rispettivo giocatore.

Oggi ho cercato di fare incrementare un solo 7segmenti dei 4 che ci sono.

Ho provato a fare l’incremento direttamente nel metodo loop() di Arduino ma non prendeva il punto al momento del click del bottone quindi sono passata a provare con attachInterrupt(), che è un metodo che permette di ‘ascoltare’ in qualsiasi momento il bottone. Il problema è che al momento del click il punteggio viene incrementato di diversi punti e non so come risolverlo.

Non riuscendo a risolverlo, ho fatto un attimo di pausa lavorando sulla documentazione e sulla presentazione, in seguito ho provato a fare l’algoritmo per il timer (conto alla rovescia) e funziona; allo scadere del tempo si accende un led e il tempo rimane a 0. Per farlo partire bisogna cliccare il bottone.

Giairo Mauro:

All’inizio abbiamo risolto il problema che avevamo con Arduino con Alessandro da un po’ di tempo.

Dopodiché ho provato a inserire il programma sull’Arduino mega con la scheda JJRobots, ma ci sono stati problemi anche per quello e ho passato la maggior parte del tempo a risolverli.

Alla fine ho provato a collegare il telefono al JJRobots per iniziare a provarlo ma ho avuto problemi anche l non ancora risolti.

Alessandro Spagnuolo:

Abbiamo risolto i problemi che avevamo con il programma di Arduino con Giairo.

Le ultime 4 ore ero assente.

Joey Biancardi:

Ho praticamente terminato la costruzione del tavolo, manca la parte del robot usata per rispondere durante la partita per un problema di stampa 3D.

Problemi riscontrati e soluzioni adottate

Giairo Mauro:

Abbiamo avuto il solito problema all’inizio con Alessandro ma siamo riusciti a risolvere cambiando alcune parti del codice fornito dalla documentazione, gli include che erano in tutti i file e dovevano essere solo in uno essendo tutti i file collegati tra loro.

Ho avuto problemi con il caricamento del codice in Arduino mega perché i file erano in una sola cartella e andavano divisi e anche una volta messi i file nelle cartelle divise come richiesto dal programma dava ulteriori errori per cui ho dovuto cancellare e riscaricare i file.

Un ultimo problema una volta caricato il programma su Arduino e non ancora risolto è il collegamento tramite Wi-Fi del telefono sul JJRobots, perché dal telefono dice che non è possibile connettersi anche se la password è quella scritta sulla documentazione.

Alessandro Spagnuolo:

Abbiamo risolto il problema con Giairo.

Punto della situazione rispetto alla pianificazione

Siamo indietro di tutto di circa 2 lezioni per i ritardi della consegna degli oggetti e gli errori, apparte con il timer.

Programma di massima per la prossima giornata di lavoro

Finire i motori e il punteggio.

Nome progetto: Form di inserimento Dati Espoprofessioni 1/1

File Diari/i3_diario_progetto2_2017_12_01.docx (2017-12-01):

# Diario di lavoro

Luogo | Scuola
Data | 01.12.2017

Lavori svolti

Alessia: le prime 3 ore sono stata impegnata nella presentazione, in seguito ho lavorato sul 7 segmenti e ho capito come funzionava.

Alle 14.45 sono andata via.

Giairo e Alessandro: Abbiamo ricevuto i pezzi per usare entrambi i motori con i driver, ci è stata data la scheda JJRobots che crea una rete Wi-Fi e permette di collegare i driver direttamente ad essa.

Abbiamo cercato i codici per utilizzare la scheda JJRobots ma le documentazioni non sono state d’aiuto.

Joey: Siccome appena iniziata la lezione sono arrivati i pezzi e il tavolo da costruire ho iniziato a montare ciò che potevo (mancano ancora un paio di parti) e nel pomeriggio dopo aver continuato questo lavoro ho risolto le saldature sbagliate della scorsa lezione, successivamente ho tagliato, limato e preparato le aste da usare per muovere il motore.

Problemi riscontrati e soluzioni adottate

Giairo e Alessandro: Durante l’utilizzo de codici abbiamo riscontrato dei problemi causati dal fatto che le documentazioni che ci sono state date ci danno dei file da installare ma non ci dicono quale aprire, in più quei file danno degli errori nella compilazione con Arduino e non siamo riusciti a trovare una soluzione, né sulle documentazioni ne su Arduino.

Punto della situazione rispetto alla pianificazione

Giairo e Alessandro: Siamo indietro per via degli§ errori riscontrati e della mancanza di aiuti nella documentazione.

Joey: Sono leggermente indietro.

Alessia: Nessun ritardo.

Programma di massima per la prossima giornata di lavoro

Joey: Finire di montare il tavolo e iniziare a dedicarmi al codice per il timer delle partite.

Alessandro e Giairo: Trovare una soluzione ali errori e provare attacco difesa e attacco-difesa.

Alessia: Finire l’algoritmo di punteggio.

Nome progetto: Form di inserimento Dati Espoprofessioni 1/1

Alessia Sarak I3AA

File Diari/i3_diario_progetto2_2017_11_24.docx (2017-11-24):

# Diario di lavoro

Luogo | SAM Trevano
Data | 24.11.17

Lavori svolti

Alessandro: ho saldato l’adafruit motor shield con i vari piedini per collegarlo ad arduino, in seguito ho installato la libreria adafruit motor shield e ho creato un progetto arduino per provare le funzionalità del motore passo-passo, ho cercato di far girare il motore come la lancetta dei secondi ma sono soltanto riuscito a farlo girare più veloce del previsto.

Giairo: All’inizio dopo aver iniziato ho fatto il file README.md del nostro repository GitHub per renderlo utile a cercare e informazioni. Ho iniziato a provare ad utilizzare il motore passo-passo con il driver “a4988 stepper motor driver” e un alimentatore esterno alla fine collegato per far partire il motore.

Alessia: Ho lavorato su come fare l’algoritmo di punteggio, quali tecniche utilizzare e quali sensori. Ho cercato perdipiù informazioni sul 7 segmenti e ho dissaldato e saldato una parte.

Joey: Inizialmente dopo aver cercato e capito il funzionamento e come vanno assemblati i display 7 segmenti, sono andato a saldare il backpack insieme al ponte per attaccare il display. Poi mi sono informato su come sono i PIN del display e come va collegato all’arduino. Infine ho scaricato le librerie da utilizzare per il corretto funzionamento e ho cercato degli esempi per capire come mostrare i diversi numeri o lettere.

Problemi riscontrati e soluzioni adottate

Alessandro: Ho riscontrato dei problemi mentre cercavo di far girare il motore come a lancetta dei secondi e il principale problema è che alle funzioni che utilizzo per far ruotare il motore posso soltanto passare un tipo INT mentre per riuscire a fare quello che volevo devo per forza passare un tipo DOUBLE o FLOAT. Non sono riuscito a trovare una soluzione a questo problema.

Giairo: Ho riscontrato problemi con il funzionamento del motore paso passo per via della poca alimentazione e i problemi a capire dove collegare i vari pin nella breadboard con il driver, il problema dell’alimentazione è stato risolto prendendo un alimentatore esterno da collegar al motore, ma ci sono ancora problemi da risolvere per quando riguarda il funzionamento effettivo del motore.

Joey: Ho saldato il backpack al ponte in maniera scorretta.

Punto della situazione rispetto alla pianificazione

In linea col gannt

Programma di massima per la prossima giornata di lavoro

Alessandro: Far funzionare i motori a nostro piacimento.

Giairo: Far funzionare il motore e iniziare a provare a programmarlo.

Alessia: Far funzionare l’algoritmo per il punteggio, che sommi i punti man mano

Joey: Dissaldare e risaldare e iniziare a lavorare al codice per il timer.

Air Ice Hockey 1/1

Alessia Sarak Alessandro Sagnuolo Giairo Mauro Joey Biancardi I3BB

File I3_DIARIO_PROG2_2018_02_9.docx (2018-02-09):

# Diario di lavoro

Luogo | Trevano
Data | 09.02.18

Lavori svolti

Alessia Sarak:

Ho perfezionato la presentazione.

Joey Biancardi:

Ho aiutato Alessia e poi sono andato via perché stavo male.

Alessandro Spagnuolo:

Ho lavorato sul programma del robot che però non funziona ancora alla perfezione.

Giairo Mauro:

Ho aiutato Alessandro con il robot e il tavolo, ho anche portato avanti la documentazione.

Problemi riscontrati e soluzioni adottate

Abbiamo riscontrato gli stessi problemi con il robot e cioè non si muove correttamente.

Punto della situazione rispetto alla pianificazione

Dato che la consegna è tra 2 settimane possiamo dire che siamo a buon punto.

Programma di massima per la prossima giornata di lavoro

Riuscire a far andare il robot correttamente.

Air Hockey 1/1

Alessandro Spagnuolo; Alessia Sarak; Joey Biancardi; Giairo Mauro I3BB

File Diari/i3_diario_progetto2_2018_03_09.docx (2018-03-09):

# Diario di lavoro

Luogo | Scuola
Data | 09.03.2018

Lavori svolti

Alessia Sarak, Joey Biancardi, Alessandro spagnuolo, Gairo Mauro:

Abbiamo lavorato alla documentazione alla presentazione e l’abbiamo provata

Giairo Mauro:

Sono stato ad “espoprofessioni” e sono arrivato la seconda ora del pomeriggio.

Problemi riscontrati e soluzioni adottate

Nessun problema

Punto della situazione rispetto alla pianificazione

Siamo in tempo dato che i professori ce ne hanno dato in più.

Programma di massima per la prossima giornata di lavoro

Nome progetto: Form di inserimento Dati Espoprofessioni 1/1

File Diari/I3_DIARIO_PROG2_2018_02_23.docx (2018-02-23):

# Diario di lavoro

Luogo | Trevano
Data | 23.02.18

Lavori svolti

Alessia Sarak, Alessandro Spagnuolo:

Abbiamo perforato dei pezzi del tavolo per permettere la funzionalità corretta di ogni componente

Joey Biancardi, Giairo Mauro:

Abbiamo lavorato sul tavolo perfezionando il codice e le sue varie costanti.

Problemi riscontrati e soluzioni adottate

Un po’ di errori con le costanti nel codice. Non fa il campo completo sia con il gioco manuale che quello automatico. Non siamo riusciti ad arrivare ad una soluzione completa.

Punto della situazione rispetto alla pianificazione

Dato che la consegna è tra 1 settimane possiamo dire che siamo a buon punto.

Programma di massima per la prossima giornata di lavoro

Riuscire a far andare il robot correttamente.

Air Hockey 1/1

Alessandro Spagnuolo; Alessia Sarak; Joey Biancardi; Giairo Mauro I3BB

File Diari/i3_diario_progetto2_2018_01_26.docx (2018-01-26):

# Diario di lavoro

Luogo | Scuola
Data | 12.01.2018

Lavori svolti

Alessia Sarak:

Ho lavorato sulla presentazione e sul montaggio degli ultimi pezzi del tavolo.

Giairo Mauro, Alessandro Spagnuolo:

Abbiamo riguardato il programma e, essendoci arrivato Arduino Leonardo, abbiamo fatto diversi test con l’applicazione, sia con la funzionalità manuale che con la videocamera ma abbiamo ancora avuto alcuni problemi.

Joey Biancardi:

Ho aiutato gli altri sia alla presentazione che con il tavolo

Problemi riscontrati e soluzioni adottate

Giairo Mauro e Alessandro Spagnuolo:

Alcuni pezzi del campo erano rotti e questo ha provocato degli errori nel funzionamento del robot, i motori che avevamo erano sbagliati quindi abbiamo dovuto cambiarli.

Punto della situazione rispetto alla pianificazione

Siamo in tempo dato che i professori ce ne hanno dato in più.

Programma di massima per la prossima giornata di lavoro

Completare il progetto.

Nome progetto: Form di inserimento Dati Espoprofessioni 1/1

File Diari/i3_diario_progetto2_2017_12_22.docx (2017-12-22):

# Diario di lavoro

Luogo | Trevano
Data | 22.12.17

Lavori svolti

Alessia: assente

Joey: lavorato sull’algoritmo del punteggio

Giairo e Alessandro: provato a utilizzare l’applicazione di JJRobots e i motori.

Giairo: Ho portato un po' avanti la documentazione.

Problemi riscontrati e soluzioni adottate

Giairo e Alessandro: problemi riguardanti il programma dato da JJRobots, i motori non si muovono e non siamo riusciti a capire il perché nemmeno con i professori

Per tutti: collegamento a internet non funzionante

Punto della situazione rispetto alla pianificazione

Siamo indietro di 3 settimane soltanto per il problema del programma JJRobots.

Programma di massima per la prossima giornata di lavoro

Mettere a posto il programma JJRobots e finire gli algoritmi di punteggio

Air Ice Hockey 1/1

Alessia Sarak, Joey Biancardi, Alessandro Spagnuolo, Giairo Mauro

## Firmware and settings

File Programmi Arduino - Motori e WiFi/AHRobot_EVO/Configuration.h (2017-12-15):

// JJROBOTS AHR AIR HOCKEY ROBOT EVO PROJECT

// USER CONFIGURATIONS HERE
// ROBOT DIMENSIONS, MAX SPEED, MAX ACCELERATION, CALIBRATION...

//#define DEBUG

// ABSOLUTE MAX ROBOT SPEED AND ACCELERATION
// THIS VALUES DEPENDS ON YOUR ROBOT CONSTRUCTION (MOTORS, MECHANICS...)
// RECOMMENDED VALUES FOR 12V POWER SUPPLY
#define MAX_ACCEL 275           // Maximun motor acceleration in (steps/seg2)/1000. Max recommended value:280
#define MAX_SPEED 32000         // Maximun speed in steps/seg. Max absolute value: 32767!!

#define MIN_ACCEL 100
#define MIN_SPEED 5000
#define SCURVE_LOW_SPEED 2500
#define SCURVE_HIGH_SPEED 28000

// Geometric calibration.
// This depends on the pulley teeth. DEFAULT: 200(steps/rev)*8(microstepping) = 1600 steps/rev. 1600/32teeth*2mm(GT2) = 25 steps/mm
#define X_AXIS_STEPS_PER_UNIT 25    
#define Y_AXIS_STEPS_PER_UNIT 25

// This is the center of the table. All units in milimeters
// This are the dimensions of the official air hockey table Exploter from Buffalo
#define TABLE_LENGTH 895
#define TABLE_WIDTH 435
#define ROBOT_CENTER_X TABLE_WIDTH/2   // Center of robot.
#define ROBOT_CENTER_Y TABLE_LENGTH/2

// Absolute Min and Max robot positions in mm (measured from center of robot pusher)
#define ROBOT_MIN_X 60
#define ROBOT_MIN_Y 58
#define ROBOT_MAX_X TABLE_WIDTH-ROBOT_MIN_X
#define ROBOT_MAX_Y ROBOT_CENTER_Y-80

// PuckSize (puck radio in mm)
#define PUCK_SIZE 22

// Initial robot position in mm
// The robot must be at this position at start time
// Default: Centered in X and minimun position in Y
#define ROBOT_INITIAL_POSITION_X TABLE_WIDTH/2
#define ROBOT_INITIAL_POSITION_Y 40   // Measured from center of the robot pusher to the table border

// Robot defense and attack lines
#define ROBOT_DEFENSE_POSITION_DEFAULT 72
#define ROBOT_DEFENSE_ATTACK_POSITION_DEFAULT 280
#define ROBOT_DEFENSE_POSITION_MIN 60
#define ROBOT_DEFENSE_POSITION_MAX 100
#define ROBOT_DEFENSE_ATTACK_POSITION_MIN 140
#define ROBOT_DEFENSE_ATTACK_POSITION_MAX 360

// CORRECTION FOR VISION SYSTEM LAG
#define VISION_SYSTEM_LAG 60   // in miliseconds

// CORRECTION OF MISSING STEPS ON MOTORS
// Coment this lines if you don´t want to make the corrections
#define CORRECT_MISSING_STEPS 1
#define MISSING_STEPS_MAX_ERROR_X 5
#define MISSING_STEPS_MAX_ERROR_Y 5
#define ROBOT_POSITION_CAMERA_CORRECTION_Y 0 // Correction of the position of the camera because the camera point of view and mark position

// PACKET SIZE (UDP MESSAGE)
#define PACKET_SIZE 12  // UDP PACKET SIZE (without sync mark), total size = PACKET_SIZE+3(sync mark)

// Utils (don´t modify)
#define CLR(x,y) (x&=(~(1<<y)))
#define SET(x,y) (x|=(1<<y))

#define RAD2GRAD 57.2957795
#define GRAD2RAD 0.01745329251994329576923690768489

#define ZERO_SPEED 65535

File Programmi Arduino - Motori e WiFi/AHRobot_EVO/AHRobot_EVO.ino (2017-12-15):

// JJROBOTS AHR: AIR HOCKEY ROBOT EVO PROJECT (Smartphone control ready!)
// Author: Jose Julio (JJROBOTS)
// Hardware: Arduino Leonardo + JJROBOTS brain shield v3 (devia)
// Date: 04/11/2015
// Last updated: 14/12/2016
// Version: 2.17
// Project page :
//   http://jjrobotos.com/air-hockey-robot-evo/
// GIT repository:
//   http://github.com/jjrobots/Air_Hockey_Robot_EVO/
// License: Open Software GPL License

#define VERSION "2.17"

// ROBOT and USER configuration parameters
#include "Configuration.h"
#include "Definitions.h"   // Variable definitions

void setup()
{
  // STEPPER PINS ON JJROBOTS BRAIN SHIELD
  pinMode(4, OUTPUT); // ENABLE MOTORS
  pinMode(7, OUTPUT); // STEP MOTOR 1 PORTE,6
  pinMode(8, OUTPUT); // DIR MOTOR 1  PORTB,4
  pinMode(12, OUTPUT); // STEP MOTOR 2 PORTD,6
  pinMode(5, OUTPUT); // DIR MOTOR 2  PORTC,6
  digitalWrite(4, HIGH);  // Disbale stepper motors

  pinMode(10, OUTPUT);  // Servo1 (arm)
  pinMode(13, OUTPUT);  // Servo2

  pinMode(A4, OUTPUT);  // Microstepping selector
  digitalWrite(A4, LOW); // 1/8 Microstepping

  pinMode(A3,INPUT);   // User puch button (pushed=>gnd)
  digitalWrite(A3,HIGH); // Enable pullup

  Serial.begin(115200);   // PC debug connection
  Serial1.begin(115200);  // ESP serial connection
  delay(5000);
  Serial.print("AHR JJRobots Air Hockey Robot EVO version ");
  Serial.println(VERSION);
  delay(1000);

  //LED blink
  for (uint8_t k = 0; k < 5; k++)
  {
    digitalWrite(13, HIGH);
    delay(300);
    digitalWrite(13, LOW);
    delay(300);
  }

  Serial.println("Initializing Wifi module...");
  // ESP Wifi module initialization routine.
  // The Robot will generate it´s own wifi network JJROBOTS_xx and listen external UDP messages...
  ESPInit();

  Serial.println("Initializing Stepper motors...");
  // STEPPER MOTORS INITIALIZATION
  // We use TIMER 1 for stepper motor 1 and Timer 3 for motor 2
  // TIMER1 CTC MODE
  TCCR1B &= ~(1 << WGM13);
  TCCR1B |=  (1 << WGM12);
  TCCR1A &= ~(1 << WGM11);
  TCCR1A &= ~(1 << WGM10);

  // output mode = 00 (disconnected)
  TCCR1A &= ~(3 << COM1A0);
  TCCR1A &= ~(3 << COM1B0);

  // Set the timer pre-scaler
  // Generally we use a divider of 8, resulting in a 2MHz timer on 16MHz CPU
  TCCR1B = (TCCR1B & ~(0x07 << CS10)) | (2 << CS10);

  OCR1A = ZERO_SPEED;   // Motor stopped
  dir_M1 = 0;
  TCNT1 = 0;

  // We use TIMER 3 for stepper motor 2
  // STEPPER MOTORS INITIALIZATION
  // TIMER3 CTC MODE
  TCCR3B &= ~(1 << WGM13);
  TCCR3B |=  (1 << WGM12);
  TCCR3A &= ~(1 << WGM11);
  TCCR3A &= ~(1 << WGM10);

  // output mode = 00 (disconnected)
  TCCR3A &= ~(3 << COM1A0);
  TCCR3A &= ~(3 << COM1B0);

  // Set the timer pre-scaler
  // Generally we use a divider of 8, resulting in a 2MHz timer on 16MHz CPU
  TCCR3B = (TCCR3B & ~(0x07 << CS10)) | (2 << CS10);

  OCR3A = ZERO_SPEED;   // Motor stopped
  dir_M2 = 0;
  TCNT3 = 0;

  delay(1000);
  TIMSK1 |= (1 << OCIE1A); // Enable Timer1 interrupt
  TIMSK3 |= (1 << OCIE1A); // Enable Timer1 interrupt

  // Enable steppers
  digitalWrite(4, LOW);

  delay(1000);

  //Initializing Robot initial position and parameters...
  position_M1 = (ROBOT_INITIAL_POSITION_X + ROBOT_INITIAL_POSITION_Y) * X_AXIS_STEPS_PER_UNIT;
  position_M2 = (ROBOT_INITIAL_POSITION_X - ROBOT_INITIAL_POSITION_Y) * Y_AXIS_STEPS_PER_UNIT;
  target_position_M1 = position_M1;
  target_position_M2 = position_M2;

  user_max_speed = MAX_SPEED;
  user_max_accel = MAX_ACCEL;
  max_acceleration = user_max_accel;
  max_speed = user_max_speed / 2;
  user_robot_defense_position = ROBOT_DEFENSE_POSITION_DEFAULT;
  user_robot_defense_attack_position = ROBOT_DEFENSE_ATTACK_POSITION_DEFAULT;
  defense_position = ROBOT_DEFENSE_POSITION_DEFAULT;   // Robot y axis defense position
  attack_position = ROBOT_DEFENSE_ATTACK_POSITION_DEFAULT;   // Robot y axis position for defense+attack

  // Output parameters to console
  Serial.print("Max_acceleration: ");
  Serial.println(user_max_accel);
  Serial.print("Max speed: ");
  Serial.println(user_max_speed);
  Serial.println("Moving to initial position...");
  Serial.println("Ready!!");

  setPosition_straight(ROBOT_CENTER_X, ROBOT_DEFENSE_POSITION_DEFAULT);

  Serial.print("Target_position:");
  Serial.print(ROBOT_CENTER_X);
  Serial.print(",");
  Serial.println(ROBOT_DEFENSE_POSITION_DEFAULT);
  //Serial.print(";");
  //Serial.print(target_position_M1);
  //Serial.print(",");
  //Serial.println(target_position_M2);

  digitalWrite(13, HIGH);
  Serial.print("AHR JJRobots Air Hockey Robot EVO version ");
  Serial.println(VERSION);
  Serial.println("ready...");

  testmode=false;
  robot_status = 0;
  timer_old = micros();
  timer_packet_old = timer_old;
  micros_old = timer_old;
}

// Main loop
void loop()
{
  int dt;
  uint8_t logOutput = 0;

  debug_counter++;

  if (analogRead(A3)<100) // pushbutton pushed => TEST PATTERN
  {
    loop_counter=0;
    testmode=true;
  }
  
  timer_value = micros();
  if ((timer_value - timer_old) >= 1000) // MAIN 1Khz loop
  {
    timer_old = timer_value;
    loop_counter++;

    packetRead();  // Check for new packets...
    if (newPacket > 0)
    {
      dt = (timer_value - timer_packet_old) / 1000.0;
      //Serial.println(dt);
      //dt = 16;  //60 Hz = 16.66ms
      timer_packet_old = timer_value;
      logOutput = 0;

      Serial.print("P");
      Serial.print(newPacket);

      if (newPacket == 1) // Camera packet
      {
        // Puck detection and trayectory prediction
        cameraProcess(dt);
        // Strategy based on puck prediction
        newDataStrategy();
        // Serial output (DEBUG)
        //Serial.print(" ");
        //Serial.print(cam_timestamp);
        //Serial.print(" ");
        //Serial.print(puckCoordX);
        //Serial.print(",");
        //Serial.print(puckCoordY);
        //Serial.print(" ");
        //Serial.print(predict_status);
        //Serial.print(",");
        //Serial.print(robot_status);
      }
      else if (newPacket == 2) { // User sends a manual move
        robot_status = 5;    // Manual mode
        Serial.print(" ");
        Serial.print(user_target_x);
        Serial.print(",");
        Serial.print(user_target_y);
      }
      else if (newPacket == 3) {
        Serial.print(" USER MAX SPEED:");
        Serial.println(user_max_speed);
        Serial.print("USER MAX ACCEL:");
        Serial.println(user_max_accel);
        Serial.print("USER DEFENSE POSITION:");
        Serial.println(user_robot_defense_position);
        Serial.print("USER ATTACK POSITION:");
        Serial.print(user_robot_defense_attack_position);
      }

      robotStrategy();

      // Robot position detection for missing steps detection in stepper motors.
      missingStepsDetection();

      Serial.println();
      newPacket = 0;
    }  // End packet received

    if (testmode)
      testMovements();

#ifdef DEBUG
    // DEBUG: We inform of the position error of the robot as seen in the camera (util for calibrations)
    if ((loop_counter % 1293) == 0) {
      Serial.print("ROBOT MSD: ");
      Serial.print(robotMissingStepsErrorX);
      Serial.print(",");
      Serial.println(robotMissingStepsErrorY);
    }
#endif

    if ((loop_counter % 10) == 0)
      updatePosition_straight();  // update straight line motion algorithm

    // Position, speed and acceleration control:
    positionControl();
  } // 1Khz loop
}

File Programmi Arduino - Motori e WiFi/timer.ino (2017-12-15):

#include <Wire.h>
#include <Adafruit_GFX.h>
#include "Adafruit_LEDBackpack.h"

Adafruit_7segment matrix = Adafruit_7segment();
const int buttonPin = 2;
const int ledPin = 9;

const int MIN_SEC_MINUTE = 0;

int mIniziale = 1;
int s1 = MIN_SEC_MINUTE;
int s2 = MIN_SEC_MINUTE;

void setup() {
  pinMode(buttonPin, INPUT);
  pinMode(ledPin, OUTPUT);
          
  #ifndef __AVR_ATtiny85__
    Serial.begin(9600);
    Serial.println("7 Segment Backpack Test");
  #endif
    matrix.begin(0x70);
}

void loop() {
   int m = mIniziale;

   matrix.drawColon(true);
   matrix.writeDigitNum(0, 0, false);
   matrix.writeDigitNum(1, m, false);
   matrix.writeDigitNum(3, 0, false);
   matrix.writeDigitNum(4, 0, false);
   matrix.writeDisplay();
   
   //Parte al click del bottone
   if(digitalRead(buttonPin)){
     int t = 60*m;
     analogWrite(ledPin, LOW);
     for(int i = 0; i < t; i++){
       //Scrive sul 7segmenti
       matrix.drawColon(true);
       matrix.writeDigitNum(0, 0, false);
       matrix.writeDigitNum(1, m, false);
       matrix.writeDigitNum(3, s1, false);
       matrix.writeDigitNum(4, s2, false);
       matrix.writeDisplay();
    
       //Conto alla rovescia
       if(s1 == MIN_SEC_MINUTE && s2 == MIN_SEC_MINUTE){
        m--;
        s1 = 5;
        s2 = 9;
       }else if(s2 == MIN_SEC_MINUTE){
        s1--;
        s2 = 9;
       }else{
        s2--;
       }
    
       delay(1000);
       if(m == MIN_SEC_MINUTE && 
         s1 == MIN_SEC_MINUTE && 
         s2 == MIN_SEC_MINUTE){
          Serial.println("STOP");
          analogWrite(ledPin, HIGH);
       }
     }
   }
}

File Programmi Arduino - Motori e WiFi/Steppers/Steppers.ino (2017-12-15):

// JJROBOTS AHR AIR HOCKEY ROBOT EVO PROJECT
// STEPPERS MOTOR CONTROL
// Updated: Now it supports DRV8825 drivers and A4988 drivers
// SPEED, ACCELERATION AND POSITION CONTROL using Arduino 16 bit Timer interrupts
// We control the speed of the motors with interrupts (Timer1 and Timer3). tested up to 32Khz.
// The position of the motor is controlled at 1Khz (in the main loop)
#include "Configuration.h"
#include "Definitions.h"
#include <Arduino.h>
#include "Arduino.h"
// TIMER 1 : STEPPER MOTOR SPEED CONTROL MOTOR1
ISR(TIMER1_COMPA_vect)
{
  if (dir_M1 == 0)
    return;

  SET(PORTE, 6); // STEP X-AXIS (MOTOR1)
  position_M1 += dir_M1;
  __asm__ __volatile__ (
    "nop" "\n\t"
    "nop" "\n\t"
    "nop" "\n\t"
    "nop" "\n\t"
    "nop" "\n\t"
    "nop" "\n\t"
    "nop" "\n\t"
    "nop" "\n\t"
    "nop" "\n\t"
    "nop" "\n\t"
    "nop" "\n\t"
    "nop");  // Wait for step pulse
  CLR(PORTE, 6);
}

// TIMER 3 : STEPPER MOTOR SPEED CONTROL MOTOR2
ISR(TIMER3_COMPA_vect)
{
  if (dir_M2 == 0)
    return;

  SET(PORTD, 6); // STEP Y-AXIS (Motor2)
  position_M2 += dir_M2;
  __asm__ __volatile__ (
    "nop" "\n\t"
    "nop" "\n\t"
    "nop" "\n\t"
    "nop" "\n\t"
    "nop" "\n\t"
    "nop" "\n\t"
    "nop" "\n\t"
    "nop" "\n\t"
    "nop" "\n\t"
    "nop");  // Wait for step pulse
  CLR(PORTD, 6);
}

// POSITION CONTROL
// We use a ramp for acceleration and deceleration
// To calculate the point we should start to decelerate we use this formula:
// stop_position = actual_posicion + (actual_speed*actual_speed)/(2*max_deceleration)
// Input parameters:
//    target_position_M1
//    target_speed_M1
//    max_acceleration

void positionControl()
{
  int32_t temp;
  uint32_t timer;
  int16_t dt;
  int16_t result_speed_M1, result_speed_M2;
  int16_t absSpeedM1, absSpeedM2;


  real_position_x = ((position_M1 + position_M2) / 2) / X_AXIS_STEPS_PER_UNIT;
  real_position_y = ((position_M1 - position_M2) / 2) / Y_AXIS_STEPS_PER_UNIT;
  //SET(PORTF,3); // for external timing debug
  timer = micros();
  // dt = delta time in microseconds...
  dt = constrain(timer - micros_old, 0, 2000); // Limit dt (it should be around 1000 most times, 1ms)
  //Serial.println(dt);
  micros_old = timer;

  // Movement accelerations...
  acceleration_M1 = max_acceleration;
  acceleration_M2 = max_acceleration;

  // Scurve profile implementation...
  absSpeedM1 = abs(speed_M1);
  absSpeedM2 = abs(speed_M2);
  if (absSpeedM1 < SCURVE_LOW_SPEED) {
    acceleration_M1 = map(absSpeedM1, 0, SCURVE_LOW_SPEED, MIN_ACCEL, max_acceleration);
    if (acceleration_M1 > max_acceleration)
      acceleration_M1 = max_acceleration;
  }
  if (absSpeedM2 < SCURVE_LOW_SPEED) {
    acceleration_M2 = map(absSpeedM2, 0, SCURVE_LOW_SPEED, MIN_ACCEL, max_acceleration);
    if (acceleration_M2 > max_acceleration)
      acceleration_M2 = max_acceleration;
  }
  // SCURVE FACOR 1900!!!

  // MOTOR1 M1
  temp = (long)speed_M1 * speed_M1;
  temp = temp / (1900 * (long)acceleration_M1);
  pos_stop_M1 = position_M1 + sign(speed_M1) * temp;    // We calculate the stop position if we apply a deceleration right now.
  if (target_position_M1 > position_M1)    // Positive move
  {
    if (pos_stop_M1 >= target_position_M1)  // Do we need to start stopping?
      result_speed_M1 = 0;                    // The deceleration ramp is done inside the setSpeed function
    else
      result_speed_M1 = target_speed_M1;      // The aceleration ramp is done inside the setSpeed function
  }
  else   // Negative move
  {
    if (pos_stop_M1 <= target_position_M1)  // Start decelerating?
      result_speed_M1 = 0;
    else
      result_speed_M1 = -target_speed_M1;
  }

  // MOTOR2 M2
  temp = (long)speed_M2 * speed_M2;
  temp = temp / (1900 * (long)acceleration_M2);
  pos_stop_M2 = position_M2 + sign(speed_M2) * temp;
  if (target_position_M2 > position_M2) // Positive move
  {
    if (pos_stop_M2 >= target_position_M2)  // Start decelerating?
      result_speed_M2 = 0;                  // The deceleration ramp is done inside the setSpeed function
    else
      result_speed_M2 = target_speed_M2;    // The aceleration ramp is done inside the setSpeed function
  }
  else   // Negative move
  {
    if (pos_stop_M2 <= target_position_M2)  // Start decelerating?
      result_speed_M2 = 0;
    else
      result_speed_M2 = -target_speed_M2;
  }

  setMotorSpeed(result_speed_M1, result_speed_M2, dt); // change Motors speed
  //CLR(PORTF,3); // for external timing debug
}

// Speed could be positive or negative
void setMotorSpeed(int16_t m1tspeed, int16_t m2tspeed, int16_t dt)
{
  long timer_period;
  int16_t accel;

  // Limit max speeds
  m1tspeed = constrain(m1tspeed, -user_max_speed, user_max_speed);
  m2tspeed = constrain(m2tspeed, -user_max_speed, user_max_speed);

  // M1 MOTOR
  // We limit acceleration => speed ramp
  accel = ((long)acceleration_M1 * dt) / 1000; // We divide by 1000 because dt are in microseconds
  if (((long)m1tspeed - speed_M1) > accel) // We use long here to avoid overflow on the operation
    speed_M1 += accel;
  else if (((long)speed_M1 - m1tspeed) > accel)
    speed_M1 -= accel;
  else
    speed_M1 = m1tspeed;

  // Check if we need to change the direction pins
  if ((speed_M1 == 0) && (dir_M1 != 0))
    dir_M1 = 0;
  else if ((speed_M1 > 0) && (dir_M1 != 1))
  {
    CLR(PORTB, 4);
    dir_M1 = 1;
  }
  else if ((speed_M1 < 0) && (dir_M1 != -1))
  {
    SET(PORTB, 4);
    dir_M1 = -1;
  }

  if (speed_M1 == 0)
    timer_period = ZERO_SPEED;
  else if (speed_M1 > 0)
    timer_period = 2000000 / speed_M1; // 2Mhz timer
  else
    timer_period = 2000000 / -speed_M1;

  if (timer_period > 65535)   // Check for minimun speed (maximun period without overflow)
    timer_period = ZERO_SPEED;

  OCR1A = timer_period;
  // Check  if we need to reset the timer...
  if (TCNT1 > OCR1A)
    TCNT1 = 0;

  // M2 MOTOR
  // We limit acceleration => speed ramp
  accel = ((long)acceleration_M2 * dt) / 1000;
  if (((long)m2tspeed - speed_M2) > accel)
    speed_M2 += accel;
  else if (((long)speed_M2 - m2tspeed) > accel)
    speed_M2 -= accel;
  else
    speed_M2 = m2tspeed;

  // Check if we need to change the direction pins
  if ((speed_M2 == 0) && (dir_M2 != 0))
    dir_M2 = 0;
  else if ((speed_M2 > 0) && (dir_M2 != 1))
  {
    CLR(PORTC, 6);
    dir_M2 = 1;
  }
  else if ((speed_M2 < 0) && (dir_M2 != -1))
  {
    SET(PORTC, 6);
    dir_M2 = -1;
  }

  if (speed_M2 == 0)
    timer_period = ZERO_SPEED;
  else if (speed_M2 > 0)
    timer_period = 2000000 / speed_M2; // 2Mhz timer
  else
    timer_period = 2000000 / -speed_M2;

  if (timer_period > 65535)   // Check for minimun speed (maximun period without overflow)
    timer_period = ZERO_SPEED;

  OCR3A = timer_period;
  // Check  if we need to reset the timer...
  if (TCNT3 > OCR3A)
    TCNT3 = 0;

}
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

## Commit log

2017-11-21 Add documenti esterni
    [623_PULEGGIA_LIBERA.stl, BASE_SUPPORTO_ASTA.stl, BOCCOLA.stl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]
2017-11-24 Ricaricato a causa di modifiche del nome.
2017-11-24 Ricaricato a causa di modifiche del nome
2017-12-15 Arduino - Motori WiFi
    [Configuration.h]
2017-12-22 Gannt Prevetivo e Consuntivo 22.12.2017
    [Analisi e Gannt.xlsx]
